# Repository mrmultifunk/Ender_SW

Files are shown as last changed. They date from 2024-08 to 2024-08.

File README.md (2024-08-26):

# Ender 3 Pro/V2 to Switchwire Conversion Release.2

This is a full conversion of the popular Ender 3 Pro/V2 to a Voron Switchwire. The motivation came from [Triano](https://github.com/walttriano) and [his awesome original conversion](https://github.com/walttriano/VoronUsers/tree/master/printer_mods/Triano/Ender_3Pro_Switchwire) that served as a starting point, however everything was re-designed from scratch (in order to follow the Voron guidelines and aesthetics more accurately). Another factor that led to this re-design, was the need to be able to enclose this printer in a, visually, pleasant and, structurally, functional way. The ingenious design of 5x MGN12H Linear Rails - 300mm (dual Y axis rail) from Triano was preserved and the printing volume is ~220x220x220.

# Release 2 Update Changelog:

- CAD files cleaned up.
- Small corrections to parts.
- Added printable deck files (still it's recommended to laser cut them though)
- Added different .dxfs for rear black panels (in case anyone wants to cut the panels from a material that is not same on both surfaces)
- Added the option to use the stock Ender 3 LCD screen.

# Rev.2 Update Changelog:

- Every change happened in order to improve the build process and the design overall.
- All screw sizes and types are properly documented in the CAD (soon there will be a conversion BOM also). Also no more “exotic” sizes, everything is according to what VORON is using officially.
- Current conversion’s enclosure is 100% compatible with the new update (except of the deck panels ofc).
- XZ Blocks improved fit for the X v-slots and are also modified to use 30mm BHCS (like the original SW).
- Y Axis, new front idler (in order to achieve a mounting point for the front grill), improved clearance for the rear Y motor mount. All use BHCS screws now.
- Split bed carriage with size and clearance corrections. Made uppon the design recommendation of Steve. Also Y belt clips have a bit more clearance on the upper side, in order to leave some space for spare belt 🙂
- XZ motors have thinner XZ tensioners to avoid the lower “split” (kudos to Steve for that ALSO).
- We are now using the original SW Spool Holder (for easier installation, due to clearance)
- Front Grills have now the LCD mount of the original SW. They also mount to the extended sides just by M3 screws.
- Rear Grills mount by M5x16 BHCS screws now. Also the inlet has moved to the side (in order to have a straight and easier connection with the PSU), this was also a recommendation by Steve and he was more than kind to share his original .F3D file. Both stock Ender and C14 inlets are compatible.
- Removed material from the grills, in order to save some plastic and cut down print time.
- PSU is now mounted parallel to the side extrusions and RS25 can be mounted in the front of the printer.
- Redesigned mounts for the Board and RPi (no more shelf and moooahr clearance!)

And last but not least…
-The side extensions. Front and rear side extensions are designed to extend the frame for aesthetical and a few practical reasons (clearance and NO MORE NOTCH). They are sturdy enough but keep in mind that you will not move around the printer by lifting it from there.

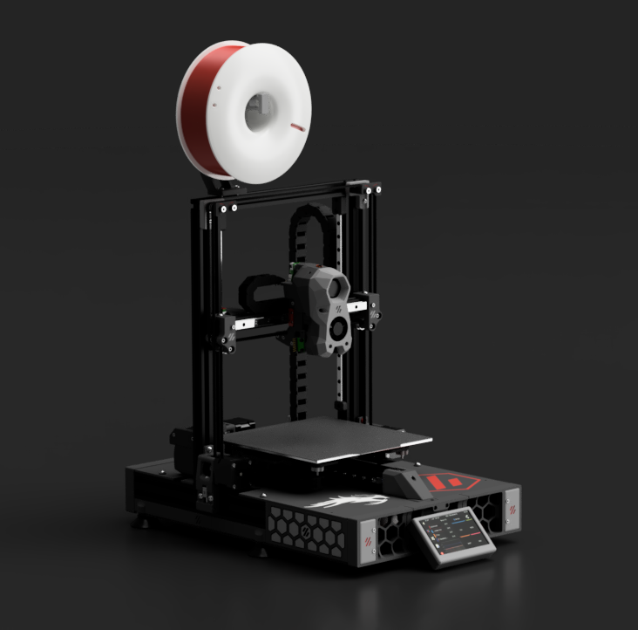
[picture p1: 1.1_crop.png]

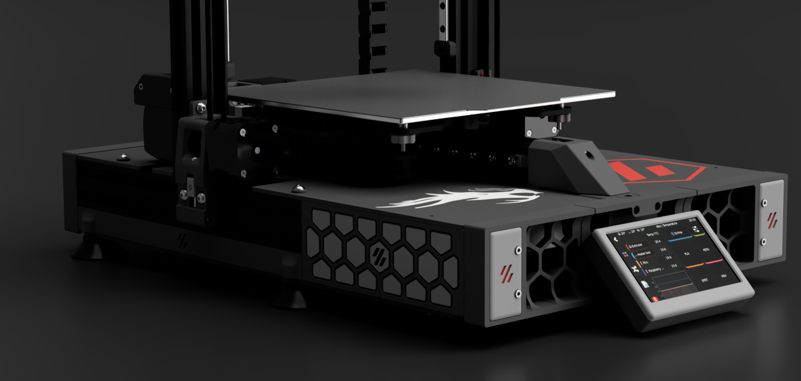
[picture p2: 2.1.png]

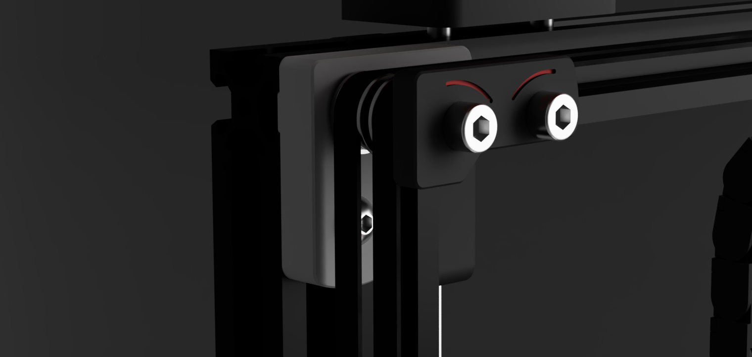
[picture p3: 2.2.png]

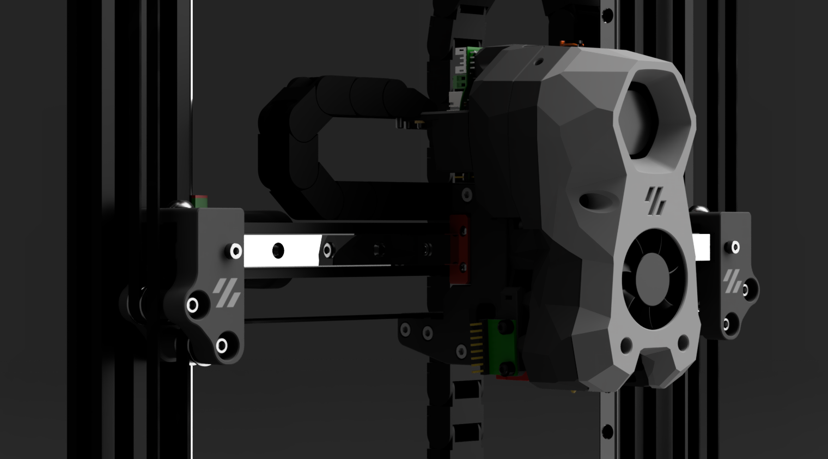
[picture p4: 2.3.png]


## Info

Various parts _can*_ be recycled from the Ender 3 Pro/V2, most important ones are:
- The frame (though a 310mm extrusion is needed for the X. You can chop the original one to length).
- The MeanWell PSU.
- The heatbed assemble.
- The original board.
- XYZ motors (as long as you can pull off the pulleys. An aftermarket 20mm motor is needed for the printhead extruder though).
- All the cables that don't go through the cable-chains (for there, silicone or PTFE cable is adviced).
- 4010 fan for the tool cooling.

*cheaping out in parts can lead into several problems, such as poor printing quality or, even worse, safety hazard. Keep that in mind and use parts from the official Switchwire BOM.

## Files

- Most of the printed part files needed for this conversion, are included in this git (you will only need to get the Stealthburner print files from the [official Switchwire git](https://github.com/VoronDesign/Voron-Stealthburner) ).
- CAD files (.f3d and .STEP) are provided, in order to help the building process, but they also serve as a BOM (in case you need to find proper screw lengths etc).
- DXF files in order to cut your enclosure panels.
- BOM (Sometime...)

## Credits

- Ofc to Triano, as his design served as base.
- To Steve (THE Steve!) for pointing out weak parts, that had to be redesigned, his tips and files and being a helpful person in general.
- To sdukan#9213 for his valuable help into troubleshooting the Ender 3 V2 differences, electronics (and in general).
- To all of this awesome community of people and especially the [ender_conversion_chat](https://discord.com/channels/460117602945990666/947303252372906014).
- To Voron design team for all the valuable resources and the solid base.

## Disclaimer

This is a very carefuly designed build.. however mistakes could have been made. By deciding to build this conversion, you are responsible for any possible damage done to the printer or even yourself.

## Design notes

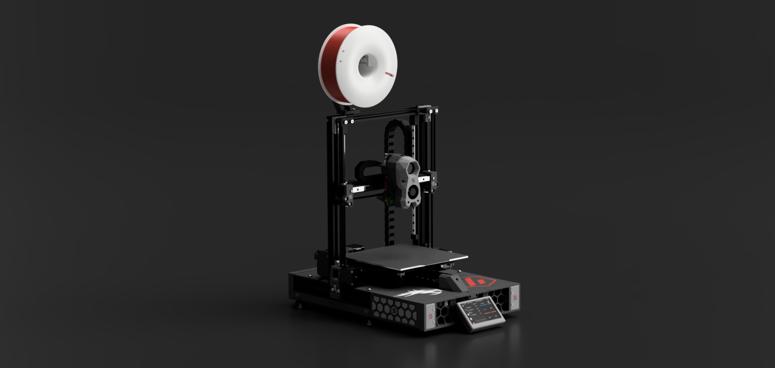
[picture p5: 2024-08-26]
1.1.png

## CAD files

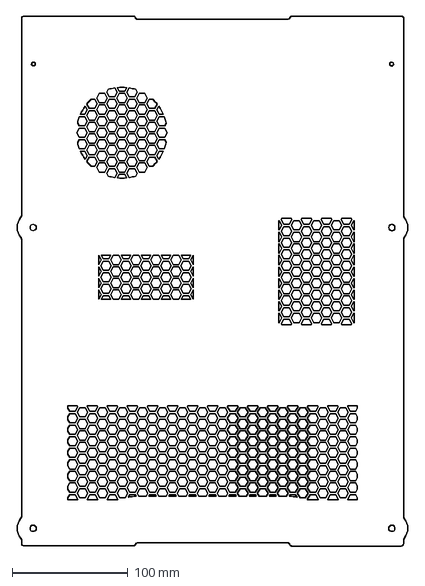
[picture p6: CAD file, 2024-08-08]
DXF/BLACK/deck_under_cut_vented.dxf
339.5 x 458.1 mm

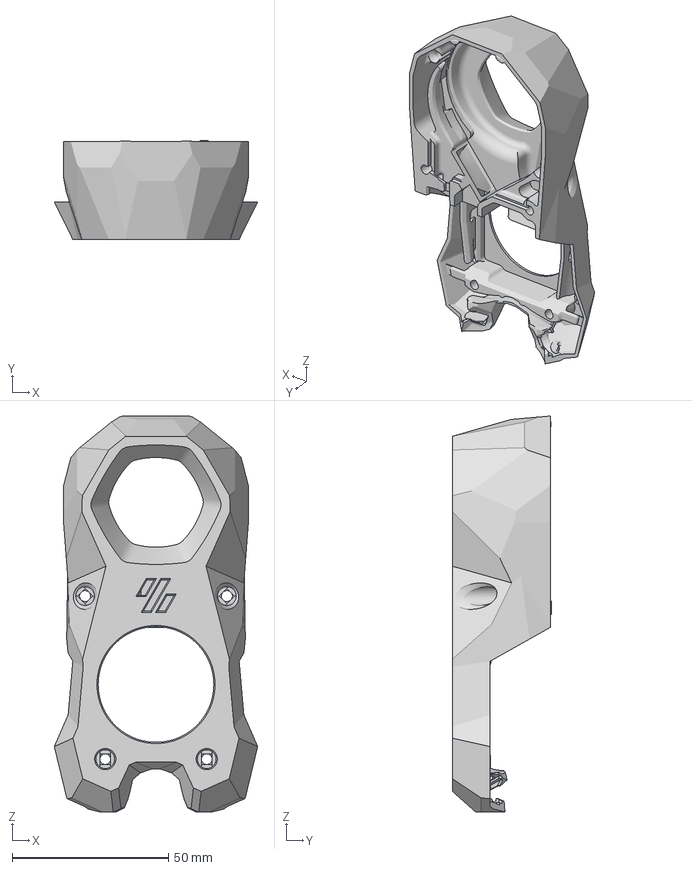
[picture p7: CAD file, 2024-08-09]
DXF/BLACK/Modified/Orbiter Stealthburner.3mf
65.1 x 31.8 x 126.8 mm

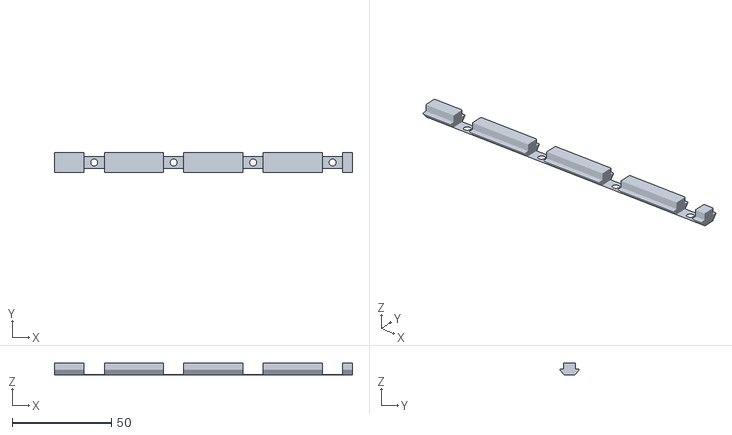
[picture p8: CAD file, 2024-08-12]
STLS/MGN9/mgn9_vslot_backer.stl
150.0 x 9.85 x 6.20

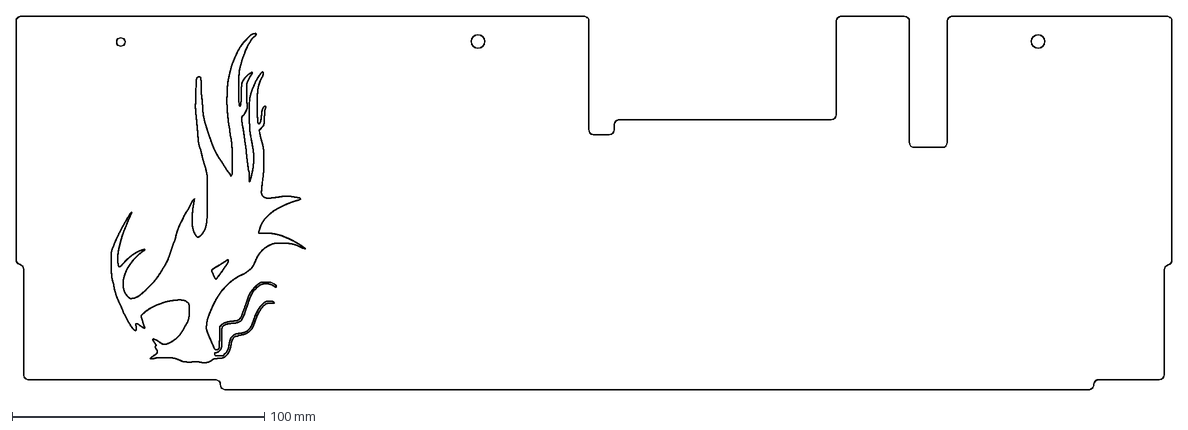
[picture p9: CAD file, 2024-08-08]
DXF/BLACK/deck_left_cut_modified.dxf
458.0 x 148.0 mm

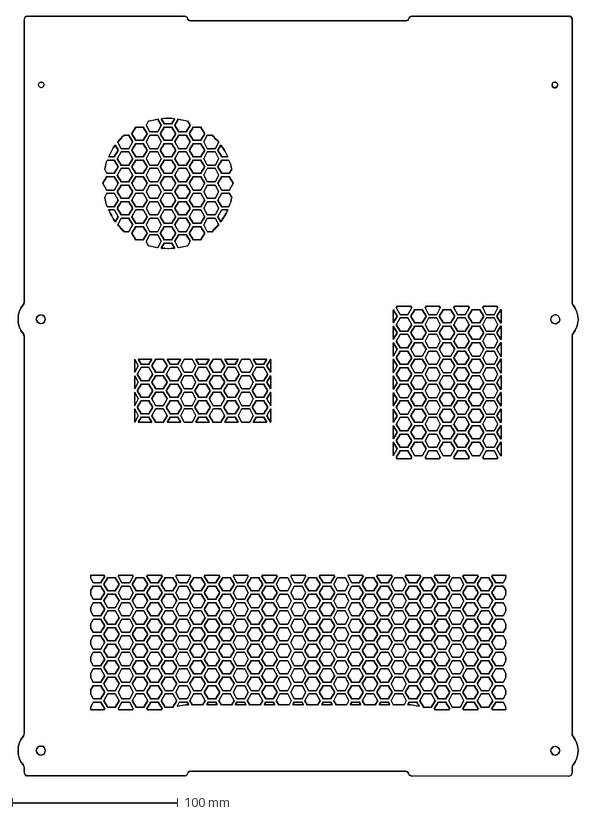
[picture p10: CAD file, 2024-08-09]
DXF/BLACK/Modified/deck_under_cut_modified.dxf
339.5 x 458.1 mm

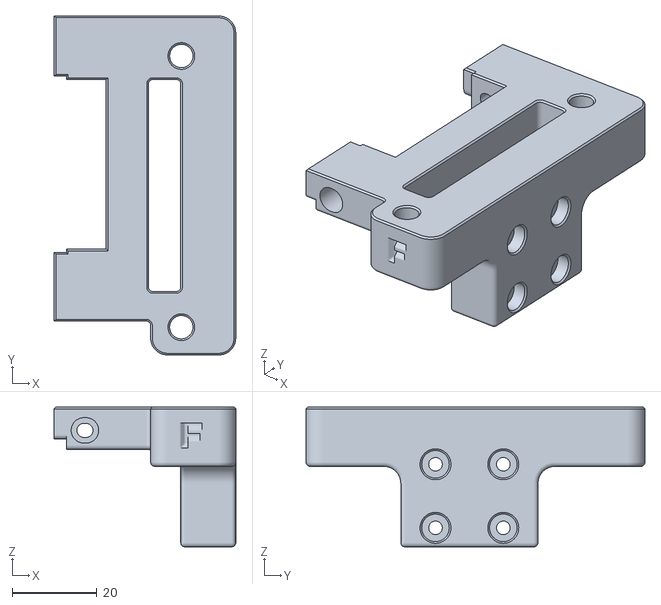
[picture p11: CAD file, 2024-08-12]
STLS/MGN9/y_axis_bed_carriage_mgn9_a.stl
42.9 x 80.0 x 33.0

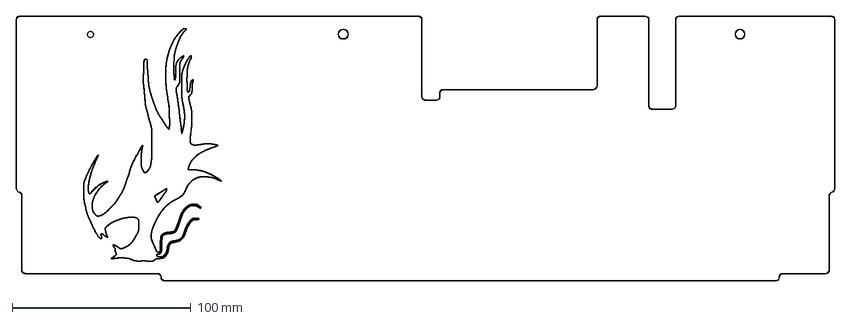
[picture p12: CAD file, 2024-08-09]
DXF/BLACK/Modified/dock_left_cut_modified.dxf
458.0 x 148.0 mm

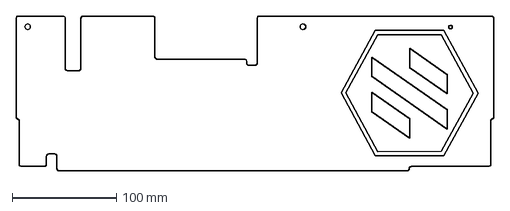
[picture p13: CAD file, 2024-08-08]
DXF/BLACK/Modified/deck_right_cut_modified.dxf
458.0 x 148.0 mm

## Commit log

2024-08-08 Edit panel files
    [bottom_panel.dxf, deck_left_cut_modified.dxf, deck_panel_left.dxf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]
2024-08-09 Add AI
    [Orbiter Stealthburner.3mf, deck_right_cut_modified.dxf, deck_under_cut_modified.dxf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]
2024-08-12 Add MGN9
    [y_axis_bed_carriage_mgn9_a.stl]
2024-08-12 Update STL
2024-08-12 Update cad
